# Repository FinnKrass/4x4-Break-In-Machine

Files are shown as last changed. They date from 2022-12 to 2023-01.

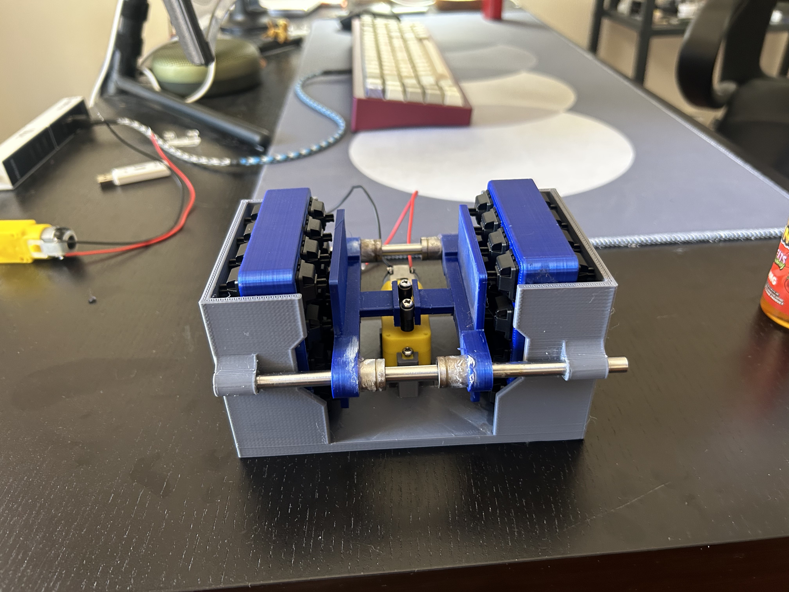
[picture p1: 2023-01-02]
Images/IMG_9655.jpg

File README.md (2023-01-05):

# Break-In-Machine-Finn

This was just sorta a project that I took on for fun, I don't think that this is perfect by any stretch of the word but it is functional and it does break the switches in. There's a heap that I wanted to add to this (caps to go over the linear bearings to secure them, off center actuation mechanism, better motor compatibility so that there was no need for the shitty ones that keep burning out), but it's taken up so much time already, and printing parts to test out a new feature can take 45 hours, so I'm gonna take a break and probably come back and start fresh with something along the lines of what flehrad designed. My point being, this is here so that people can use it as a base for future stuff, or just for people to print a basic machine that works out of the gate, it probably won't be updated very much though. 

https://youtube.com/shorts/gvkfs5RNUaU

Here is the BoM:

Prints:
  - 1* Machine Housing - best suited to pla+ or petg, a prototype I did in standard pla was pretty flimsy
  - 2* Actuation Plates - any material really, I did pla+ and that worked without a single issue
  - 1* Scotch Yoke - I personally printed 30 of these since they kept breaking even when printed with petg. Then I decided to print at 0.1 layer height and now the motor seems like it runs better and there hasn't been a single failure.
  - 2* Switch plates - Would say print these in whatever, use lightning infill at a higher percent if you really want to speed these up.

Items: I recommend buying extras of all
  - 2* 6mm x 150mm smooth rod (example https://www.makerstore.com.au/product/hard-rod-6/ )
  - 4* 6mm Linear bearings (example https://www.makerstore.com.au/product/bear-lm6uu/ )
  - 2* 0306 needle bearing (example https://appliedau.com.au/product-details/bearings/roller-bearings/needle-roller-bearings/hk-0306-tn/9e46f232-d7c0-11ea-9e6c-567e73c68856)
  - As many as you want* 1:48 TT Geared Motor 3-6v OR 1:90 All Metal Gearbox TT Motor. Don't waste your time and money on the cheap ones from amazon, you will get anywhere between 5 minutes and 3 hours of use before they die https://core-electronics.com.au/dc-gearbox-motor-tt-motor-200rpm-3-to-6vdc.html)
  - 1* M3x6 Screw
  - 2* M3x20 Screw
  - 2* M3x10 Screw
  - 2* M3x14 Screw

I just printed a more final version of the machine at .15 and .1 layer height depending on the required strength for the part and that has been the best performing one I have made so far.

I used a power supply unit which allows me to control the voltage of the machine, I saw the thing get up to a maximum speed of 650rpm but I wouldn't do that or you'll burn the motor out in under an hour, I did so just to see how long it could run.

I would implore others to use this as a base of reference, this is so so far from a completed and thorough/reliable design. It definitely works, and it works well at that, but it isn't end user friendly at all which was not the intention of this project!!

Assembly is pretty straight forward.
  - Place the scotch yoke on the motor, screw it into place with the M3x6 screw and then attach the 0306 bearings on either end with M3x10 screws
  - Secure the motor to the housing with 2 M3x20 and 1 M3x14
  - Insert the 6mm Linear bearings into the plates, I used a small hammer and tapped them lightly to ensure they were snug and fully in. They did end up coming loose after a couple days of using the machine so I just put them in so that they were in the socket but only the tip, surrounded it with superglue, pushed the whole thing in and let it dry. 
  - Insert smooth rod 1/3 into the guide holes on each side then place the first plate on, push the rod in 2/3 and insert the second plate, then push the rod the full way. I used a hammer to lightly tap the rods in.

Any questions shoot me a dm on discord @ Finn#0381

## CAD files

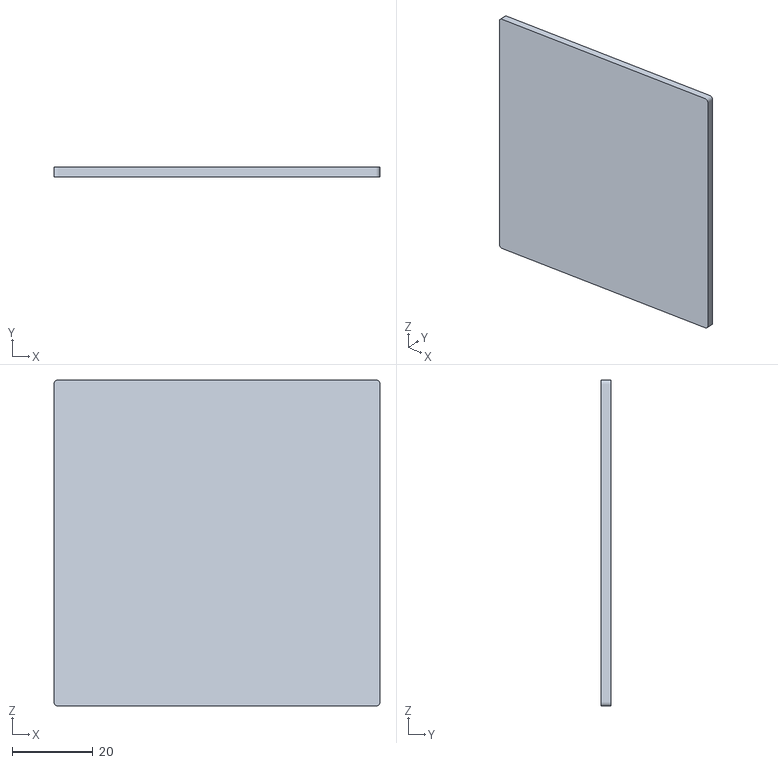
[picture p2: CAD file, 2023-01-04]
NK-Cream-Spacer.stl
81.0 x 2.40 x 81.0

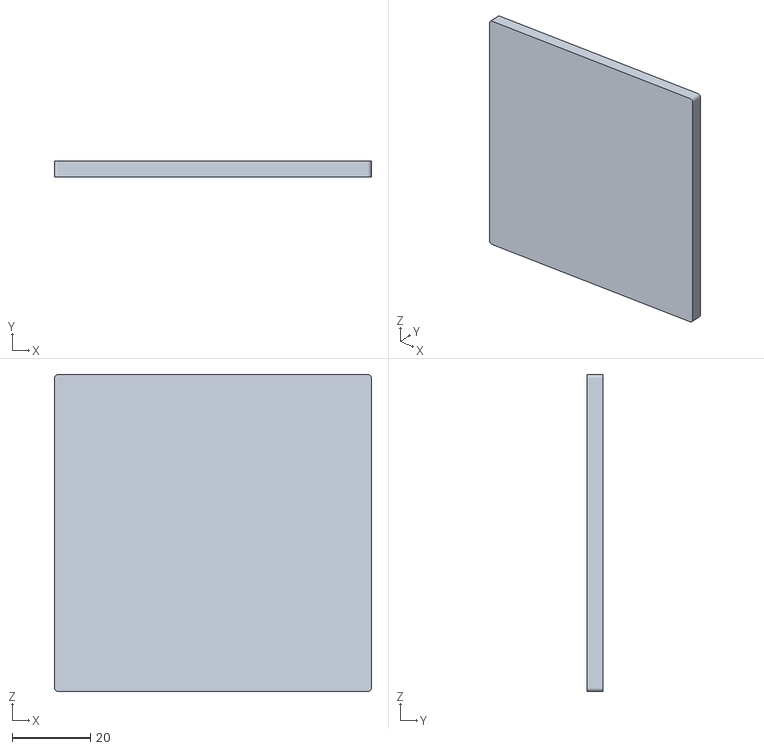
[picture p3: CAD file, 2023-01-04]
Standard Spacer.stl
81.0 x 4.00 x 81.0

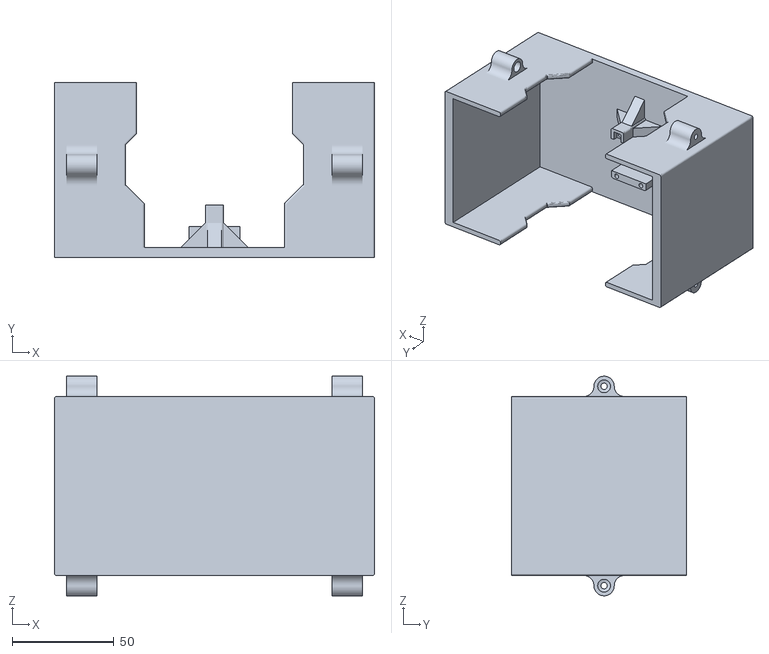
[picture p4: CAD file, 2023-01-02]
Machine Housing.stl
157.3 x 86.0 x 108.0

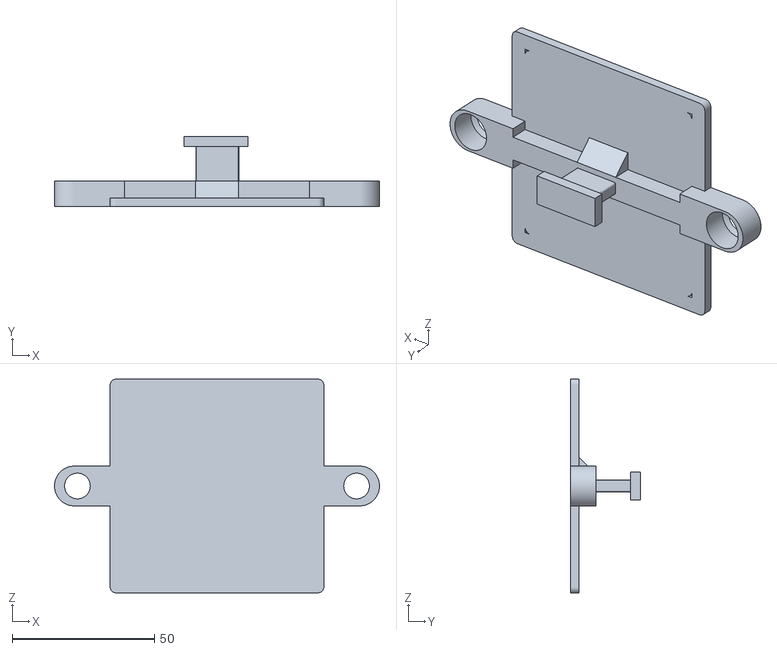
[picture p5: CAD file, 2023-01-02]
Actuation Plate.stl
114.1 x 24.5 x 75.0

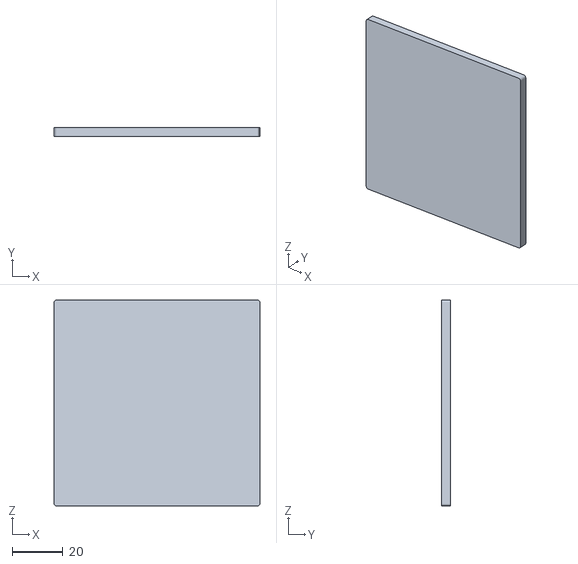
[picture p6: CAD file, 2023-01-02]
3.5mm-Spacer.stl
81.0 x 3.50 x 81.0

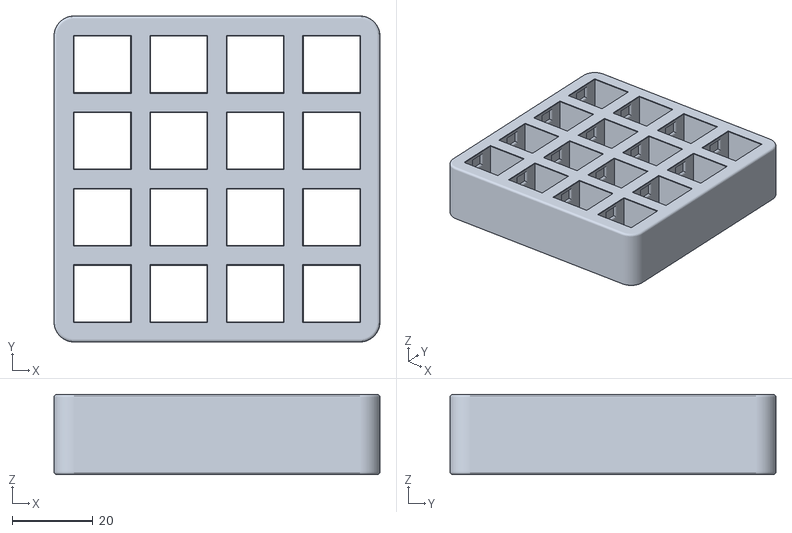
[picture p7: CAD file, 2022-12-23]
4x4 Switch Plate.stl
81.0 x 81.0 x 20.0

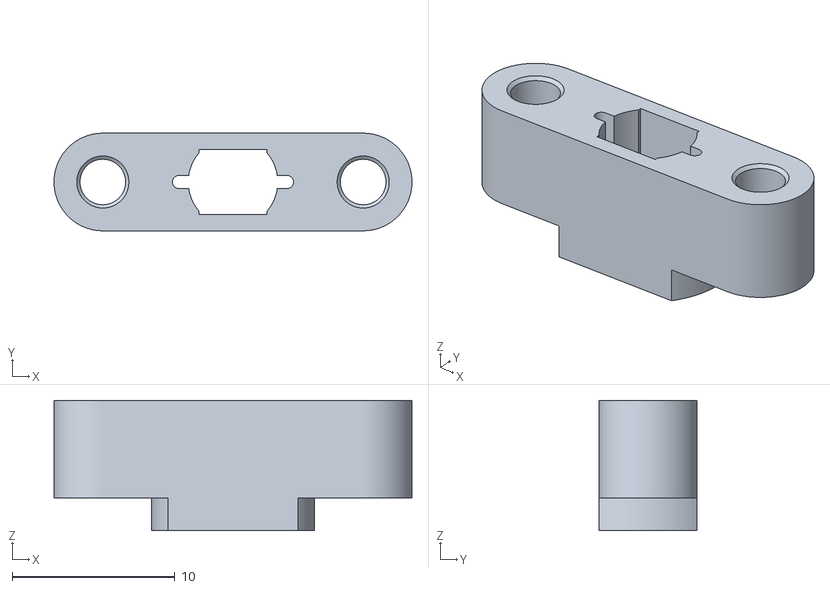
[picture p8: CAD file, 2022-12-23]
Scotch Yoke.stl
22.0 x 6.00 x 8.00

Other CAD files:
4mm-Spacer.stl

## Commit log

2022-12-23 Create 4x4 Switch-Plate.stl
    [4x4 Switch-Plate.stl]
2023-01-04 Updated Spacers
    [3.5mm-Spacer.stl, 4mm-Spacer.stl, NK-Cream-Spacer.stl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]
